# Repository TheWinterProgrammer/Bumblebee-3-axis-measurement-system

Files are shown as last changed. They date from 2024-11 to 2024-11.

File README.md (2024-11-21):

# Bumblebee 3-Axis Measurement System

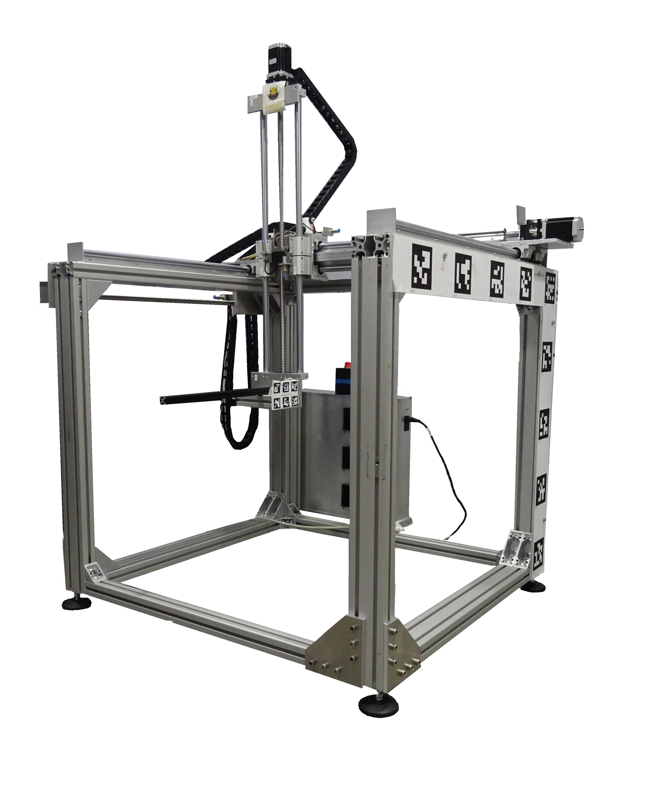
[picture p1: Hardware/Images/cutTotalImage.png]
  

## Overview

The **Bumblebee 3-Axis Measurement System** is a versatile, open-source, cubic positioning robot adapted for low-field MRI research. This project builds upon the design of the original [COSI Measure Robot](https://www.opensourceimaging.org/project/cosi-measure/), enhancing its mechanical and electronic capabilities. The system was redesigned during the 2023-2024 academic year as part of several bachelor theses at our institute.

### Key Features
- **Adapted Mechanical Design**  
  The robot is designed for:
  - A larger measurement volume.
  - Improved efficiency relative to the robot's size.

- **Simplified Electronics**  
  Replacing the BeagleBone Black and embedded Linux system, the new design features:
  - An **Arduino MEGA** as the central microcontroller for motor control, limit switch evaluation, and serial communication.
  - A **Python-based host PC script** to:
    - Control mapping.
    - Communicate positions to the robot.
    - Interface with the Hall sensor.

- **Sensor Integration**  
  The current setup uses the **F.W. BELL Series 9900 Hall sensor** with the ZOA99-3208 3D Hall probe. The Python script processes data from this sensor via serial communication. However, the system can accommodate other sensors as needed.

---

## Publication

This work was presented and published as a conference paper:  
**Samlow J, Maltsev S [TheWinterProgrammer](https://github.com/TheWinterProgrammer), Buckenmaier K, Scheffler K, Povolni P [ppolGTMonster](https://github.com/ppolGTMonster) (2024). Easy Rebuildable Cubic 3-Axis Positioning Robot Based on Open-Source Hardware: Validated via Camera-Based Motion Tracking and Initial Application in Magnetic Low Field Mapping.** *DACH-ISMRM 2024 Program & Proceedings, Tübingen, Germany*, pp. 1–2.

---

## Getting Started

There a tree major parts:

### System Components
1. **Hardware** [here](Hardware)
   - Rebuilt mechanical design for larger volume mapping.
   - Compact yet efficient cubic robot frame.

2. **Electronics** 
   - Arduino MEGA for robot control and interfacing [here](Software/Arduino/).
   - Support for various sensors through serial communication.

3. **Software** [here](Software/PythonGUI/)
   - Python script to manage mapping and communication.

### Usage
1. Set up the Arduino MEGA and connect the motors, limit switches, and Hall sensor.
2. Run the Python script on the host PC for:
   - Position control of the robot.
   - Real-time data collection from the Hall sensor.

---
## Author
   - Judith Samlov ([E-Mail](judith.samlov@tuebingen.mpg.de)), (Hardware and Software) 
   - Pavel Povolni ([E-Mail](pavel.povolni@tuebingen.mpg.de), [Github](https://github.com/ppolGTMonster)), (Hardware and Software)
   - Sergej Maltsev ([E-Mail](sergej.maltsev@tuebingen.mpg.de), [Github](https://github.com/TheWinterProgrammer)), (Software Python GUI)

### Contact
For further inquiries or contributions, feel free to reach out through the repository.

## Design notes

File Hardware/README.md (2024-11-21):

# Hardware

## Assembly Robot

The assembly of the robot, including all CAD design files and instructions, is thoroughly described and documented in the following resources:  
- [COSI Measure Project Page](https://www.opensourceimaging.org/project/cosi-measure/)  
- [COSI Measure GitHub Repository](https://github.com/opensourceimaging/cosi-measure/tree/master/Mechanical%20System)  

We recommend referring to these resources for detailed instructions. The hardware components for the drive and ordering details are also described there.

### Key Components for 3D Drive
We used the following parts for the 3D drive. These may be relevant if adapting the PCB, though similar drives should also work:

- **Motor**: NEMA23 60HS88, 3 pieces (no longer available)  
  Alternative: [HYBRID NEMA-23 Stepper Motor](https://www.reichelt.de/hybridschrittmotor-nema-23-1-8-4-2-a-2-52-v-act-23hs9440-26-p316758.html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)  
- **Motor Driver**: ACT DM542, 3 pieces  
  Link: [Stepper Motor Driver ACT DM542](https://www.reichelt.de/schrittmotortreiber-fuer-nema-23-18-50-v-act-dm542-p237924.html?&trstct=pos_1&nbc=1)  
- **Limit Switch**: LJ12A3-4-Z/BX DC6-36V, 3 pieces  
  Link: [Inductive Sensor](https://www.roboter-bausatz.de/p/induktiver-sensor-lj12a3-4-z-bx-dc6-36v?number=RBS11420)  
- **Power Source**: 36V, 9.75A (350W)  
  Link: [36V Power Supply](https://www.reichelt.de/schaltnetzteil-geschlossen-351-w-36-v-9-75-a-mw-uhp-350-36-p256082.html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)  

---

## Assembly PCB

### General

For this version of COSI Measure, we used an **Arduino Mega** as the central microcontroller (µC).  

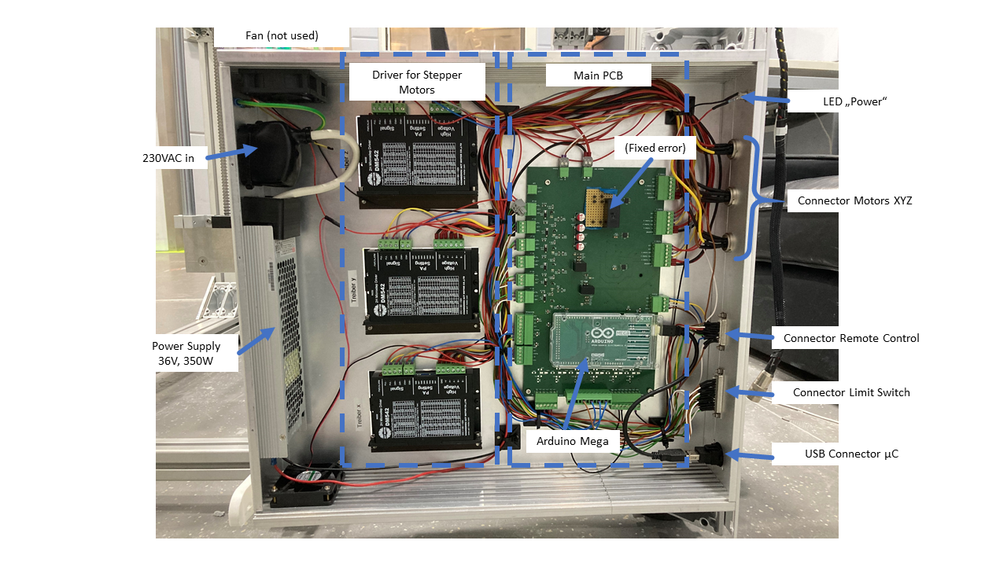
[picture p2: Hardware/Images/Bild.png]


While assembling, some errors in the V1.0 PCB design were identified and corrected in version V2.0, which is made available here.  

This design uses a two-part concept:  
1. **Main PCB**  
2. **Optional Remote Control**  
   - The remote control can manually adjust the Hall sensor's position. Although the remote control functionality was disabled in this setup, the buttons and encoders remain available in the hardware. Manual control has been replaced by Python-based software control.

If needed, you can design your own remote control and connect it via the 26-pin SubD connector.

### Implemented Functions

- Control of 3 stepper motors via PWM signals.  
- Safety circuit with emergency stop to disconnect motor drivers' power supply.  
- I2C output, e.g., for display integration.  
- Serial communication (USB) with the host PC.  
- Other analog inputs/outputs are available and can be used e.g. for additional sensors.

### PCB Design
- Designed using **KiCad 8** (no additional packages required).  
- Comments in the schematic provide explanatory details.  
- Uses large SMD components (e.g., SMD1206 for resistors and capacitors) for easy soldering.  
- Two-layer PCB design to reduce manufacturing costs.  
- A bill of materials (BoM) is included in the accompanying Excel sheet.  

#### Note
The PCB size can be reduced by modifying component footprints and minimizing unused connectors.

### Assembly PCB
- Large component sizes simplify soldering.  
- Arduino Mega connects via pin headers for easy replacement.  
- A cutout in the PCB allows visibility of the Arduino's built-in LED when mounted.  

### Wiring Inside the Case
The PCB, power supply, and motor drivers are all housed in a single case. Wiring is straightforward with labeled connectors on the PCB. **Phoenix 3.81mm PCB connectors** were used to facilitate cable attachment.  

#### ⚠️ Important Safety Note:
<span style="color: red;">- The power supply operates at 230V AC, which is **extremely dangerous**.</span>  
<span style="color: red;">- Electrical connections between the power input and power supply are **not documented here**.</span>  
<span style="color: red;">- **Only a qualified electrician** should handle this part. Ensure the case is grounded and use an FI-protected socket.</span>

---

## Assembly Case for Electronics

### Case Design
The case is a standard **19-inch, 2 height units** enclosure. The side profiles, front and back panels, and top and bottom panels were milled using a mechanical workshop.  

For best results, the front and back panels should be milled. Alternatively, mounting holes can be created manually. Accuracy is essential for mounting the DSub connector.  

Cooling: Two 12V fans were installed but found unnecessary during operation. Drivers were mounted on the base plate with cooling fins extending outward for heat dissipation. However, this may not be required.

### CAD Files
The case design was created using **Autodesk Inventor 2022**.  
- Files are exported as STEP files for compatibility with other CAD programs.  
- Side profiles are customizable, depending on the electronics installed.  

### Front Connections
All parts for the front panel are listed in the BoM.  
- **USB**: For Arduino Mega-PC serial communication.  
- **Limit Switches**: 25-pin Sub-D (male) for connecting up to 6 limit switches.  
- **Remote Control**: 26-pin Sub-D (female).  
- **Motor Connections**: 4-pin DIN connectors (male) for X, Y, and Z-axis motors.  
- **Power LED**: Indicates power supply status.  
- **Emergency Stop**: Cuts power to motor drivers via relay.  

### Back Connections
- **230V IEC Plug**: Includes an on/off switch and main fuse (1.75A, slow-blow).  

### Wiring
Wiring is simplified by labeled PCB connectors and depends on the components installed. For questions, please contact us.

---

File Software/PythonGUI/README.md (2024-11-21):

# Python GUI Software

## Overview

This script opens a GUI to operate the **3-Axis Measurement System**, create a measurement point structure, and evaluate a measured magnetic field.

### Key Features
- **Adapted Program Design**  
  This Program is designed for:
  - Movement of the Robot, by a Serial connection.
  - Creation of a point array for different shapes.
  - Automatic measurement of the points array with also saves the Hall sensor data.
  - An optional activation of a Relay during the measurement, e.g. to measure a current dependent system.
  - Evaluation of a measurement with plot a histogram of the gradient magnetic field or a homogeneous field.

- **Tab Design**  
  The Tabs in this Program are designed like:
  - **Measurement Tab**: This Tab controls the robot, relay and Hall sensor by 3 different Serial connections:  
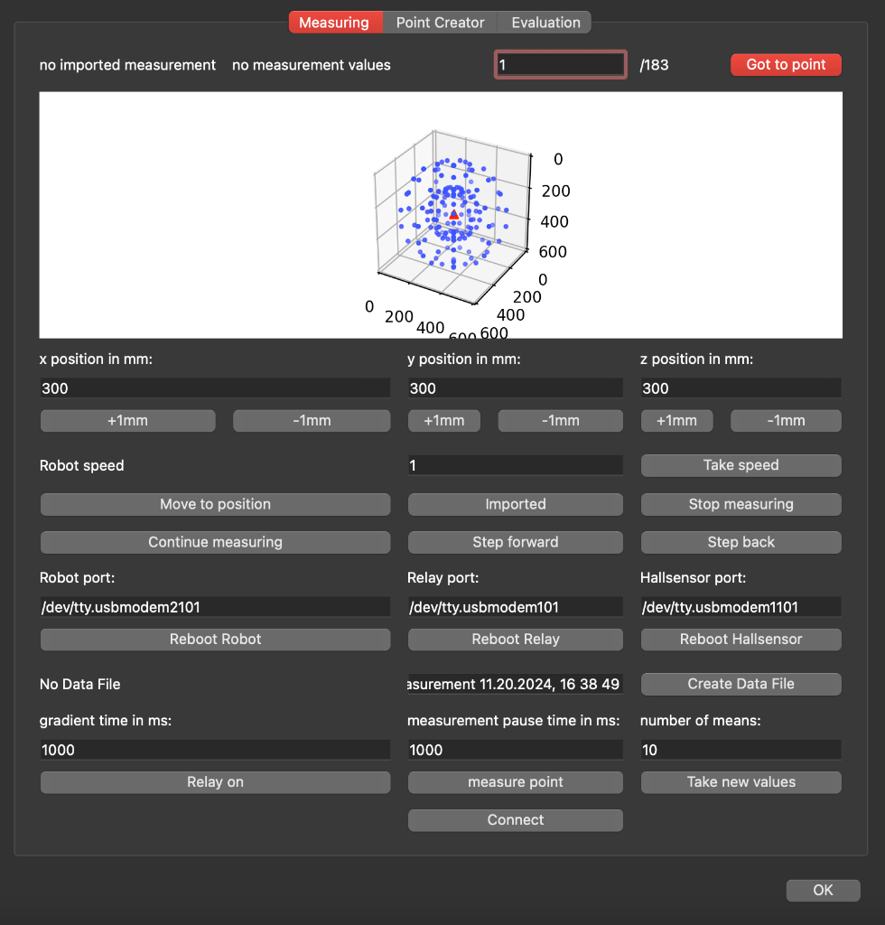
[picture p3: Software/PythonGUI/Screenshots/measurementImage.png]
      
  - **Point Creator Tab**: This Tab creates a Measurement CSV file, which can be implemented into the Measurement Tab, to start a measurement through it:  
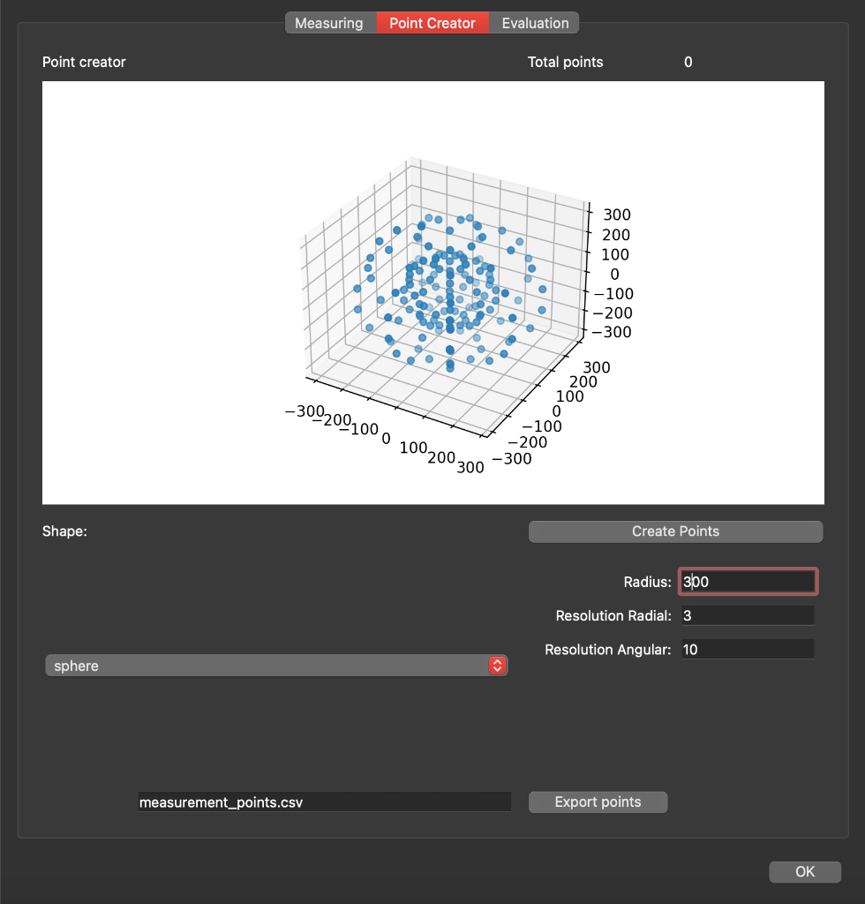
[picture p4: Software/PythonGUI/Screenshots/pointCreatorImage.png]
      
  - **Evaluation Tab**: In this Tab you can make a simple evaluation:  
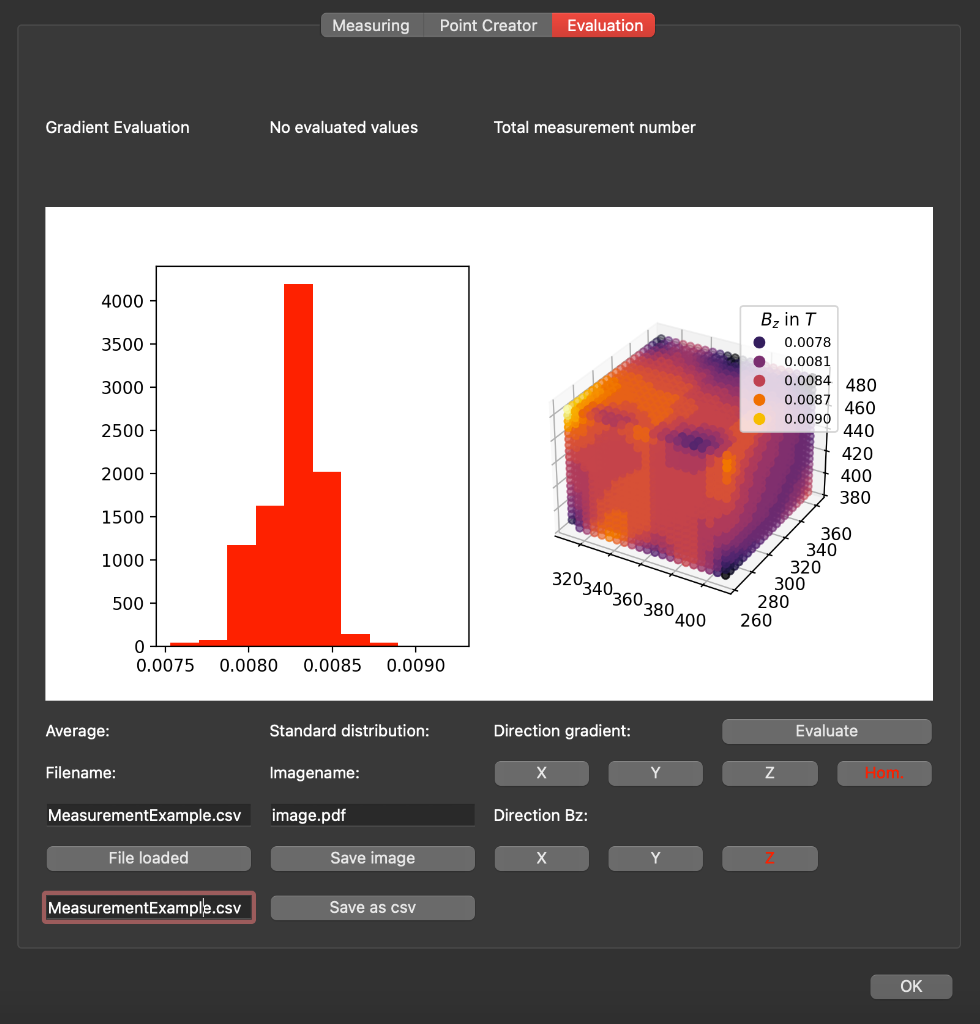
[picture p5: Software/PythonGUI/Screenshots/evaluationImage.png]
      

## Get Started

You need Python **3.8** or newer. Follow these steps to set up and run the software:

### 1. Create a Virtual Environment (Recommended)

1. Open your terminal or command prompt.
2. Navigate to the project directory:
   ```bash
   cd path/to/project
   ```

3. Create a virtual environment:
  ```bash
  python3 -m venv myenv
  ```

4. Activate the virtual environment:
 - On macOS/Linux:
    ```bash
    source myenv/bin/activate
    ```

- On Windows:
    ```bash
    myenv\Scripts\activate
    ```

### 2. Get the required libraries
Download the required libraries:
```bash
pip install -r requirements.txt
```
### 3. Run the Software
1. Start the program with the following command:
  ```bash
  python ALFRobotSoftware.py
  ```
  or
  ```bash
  python3 ALFRobotSoftware.py
  ```

2. The GUI will open, and you can begin using the application.

### Contact
For further inquiries or contributions, feel free to reach out through the repository.

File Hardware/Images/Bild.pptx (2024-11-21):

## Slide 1

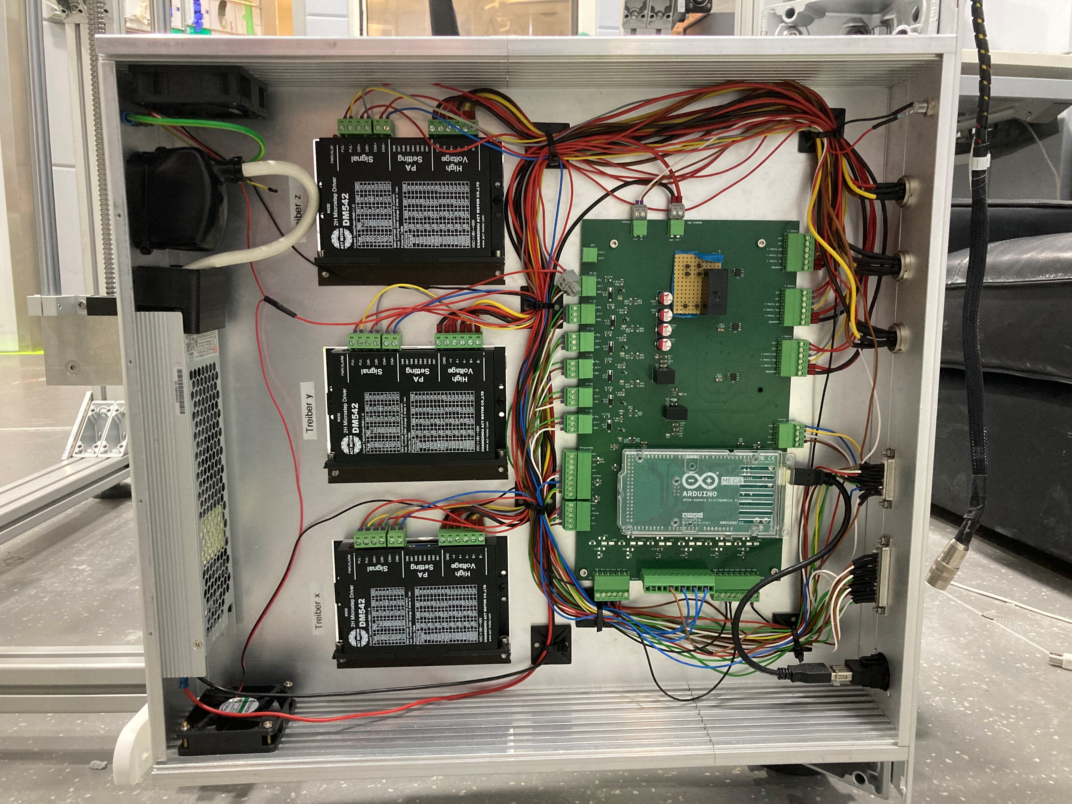
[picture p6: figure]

Fan (not used)

Driver for Stepper Motors

Main PCB

Arduino Mega

LED „Power“

(Fixed error)

230VAC in

Connector Motors XYZ

Connector Remote Control

Power Supply
36V, 350W

Connector Limit Switch

USB Connector µC

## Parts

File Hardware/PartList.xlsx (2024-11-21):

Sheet: PCB
Order list for electronic components
ID | Part-Info | Manufacturer | Part# Manufacturer | Part# Mouser | Amount | Comment
U1 | DCDC 12V, 2A | CUI Inc | P7812-2000-S | 490-P7812-2000-S | 1 | could be any cheaper option
U2 | DCDC 5V, 2A | TRACO Power | TSR 2-2450 | 495-TSR2-2450 | 1 | could be any cheaper option
K3 | Relais 12V, 16A | CUI Devices | PR22-12V-400-1A | 179-PR22-12V-400-1A | 1
D6, D9, D10, D13, D14, D17, D18 | Zener Diode 5.1V | Diodes Inc | SMAZ5V1-13-F | 621-SMAZ5V1-F | 7
D30,D24.D23,D31,D25,D29,D22,D27,D21,D26,D19,D28 | Zener Diode 5.1V | -''- | -''- | -''- |  | Backup Place, if needed
C4,C3,C1,C2 | Pol C 100uF, 50V | Wurth Electronic | 865080653016 | 710-865080653016 | 4
C10,C5,C11, C14,C33,C13,C12,C32,C31 | C 100nF, SMD1206 | KEMET | C1206C104M5RACTU | 80-C1206C104M5R | 9
C36,C34,C35,C6 | C 10nF, SMD1206 | Wurth Electronic | 885012208112 | 710-885012208112 | 4
C8,C7 | C 22uF, SMD1206 | Murata | GRM31CC71E226ME15L | 81-GRM31CC71E226ME5L | 2
C9 | C 10uF, SMD1206 | Samsung Electro-Mechanics | CL31A106KAHNNNF | 187-CL31A106KAHNNNF | 1
Q1, Q4,Q3,Q6,Q2,Q5,Q7 | nFET, 60V, 300mA | Vishay | 2N7002K-T1-GE3 | 781-2N7002K-GE3 | 7 | could be any cheaper option
D5,D2,D3,D1 | LED Blue, SMD0603 | Wurth Electronic | 150060BS75000 | 710-150060BS75000 | 4
D11,D12 | LED Red, SMD0603 | Wurth Electronic | 150060RS75000 | 710-150060RS75000 | 2
D16,D15 | LED Green, SMD0603 | Wurth Electronic | 150060GS75000 | 710-150060GS75000 | 2
D8,D7 | LED Yellow, SMD0603 | Wurth Electronic | 150060YS75000 | 710-150060YS75000 | 2
U3,U4,U5 | Current Sensor | Texas Instruments | TMCS1107A4BQDT | 595-TMCS1107A4BQDT | 3
D4 | Diode, SMD1206, 1A | Comchip Technology | CURN105-HF | 750-CURN105-HF | 1
R7, R11,R10,R8,R12,R9,R13 | R 10kOhm, SMD1206 | ROHM Semicon | SFR18EZPJ103 | 755-SFR18EZPJ103 | 7 | could be any cheaper option, aslo smaller if PCB is redesigned
R6 | R 82kOhm, SMD1207 | Bourns | CR1206-JW-823ELF | 652-CR1206JW-823ELF | 1 | could be any cheaper option, aslo smaller if PCB is redesigned
R1,R5 | R 1.8kOhm, SMD1208 | Bourns | CR1206-FX-1801ELF | 652-CR1206FX-1801ELF | 2 | could be any cheaper option, aslo smaller if PCB is redesigned
R4, R26,R35,R27,R18,R19,R34 | R 470kOhm, SMD1209 | Bourns | CR1206-FX-4703ELF | 652-CR1206FX-4703ELF | 7 | could be any cheaper option, aslo smaller if PCB is redesigned
R2 | R 500Ohm, SMD1210 | Vishay | MCA12060D5000BP500 | 594-MCA12060D5000BP5 | 1 | could be any cheaper option, aslo smaller if PCB is redesigned
R33,R3,R32 | R 100Ohm, SMD1211 | Bourns | CR1206-JW-101ELF | 652-CR1206JW-101ELF | 3 | could be any cheaper option, aslo smaller if PCB is redesigned
R14,R15,R30,R23,R31,R22 | R 1kOhm, SMD1212 | Vishay | CRCW12061K00JNEAC | 71-CRCW12061K00JNEAC | 6 | could be any cheaper option, aslo smaller if PCB is redesigned
R25,R24,R16,R17 | R 150Ohm, SMD1213 | Bourns | CR1206-JW-151ELF | 652-CR1206JW-151ELF | 4 | could be any cheaper option, aslo smaller if PCB is redesigned
R21,R28,R20,R29,R36,R37 | R 49.9kOhm, SMD1214 | Yageo | RT1206FRE0749K9L | 603-RT1206FRE0749K9L | 6 | could be any cheaper option, aslo smaller if PCB is redesigned
Ard1 | Arduino Mega | Arduino | A000067 | 782-A000067 | 1 | could be any cheaper option
Connectors
J10, J11, J5, J8 (Male) | 2pin | Phoenix Contact | 1803277 | 651-1803277 | 4 | PCB Thorugh Hole Mount
Female |  | Phoenix Contact | 1803578 | 651-1803578 | 4 | Wire Mount
J12, J13, J14, J15, J16, J17 (Male) | 3pin | Phoenix Contact | 1803280 | 651-1803280 | 6 | PCB Thorugh Hole Mount
Female |  | Phoenix Contact | 1803581 | 651-1803581 | 6 | Wire Mount
J1 (Male) | 4pin | Phoenix Contact | 1803293 | 651-1803293 | 1 | PCB Thorugh Hole Mount
Female |  | Phoenix Contact | 1803594 | 651-1803594 | 1 | Wire Mount
J19 (Male) | 5pin | Phoenix Contact | 1803303 | 651-1803303 | 1 | PCB Thorugh Hole Mount
Female |  | Phoenix Contact | 1803604 | 651-1803604 | 1 | Wire Mount
J2, J6, J7, J9 (Male) | 6pin | Phoenix Contact | 1803316 | 651-1803316 | 4 | PCB Thorugh Hole Mount
Female |  | Phoenix Contact | 1803617 | 651-1803617 | 4 | Wire Mount
J4, J18 (Male) | 8pin | Phoenix Contact | 1803332 | 651-1803332 | 2 | PCB Thorugh Hole Mount
Female |  | Phoenix Contact | 1803633 | 651-1803633 | 2 | Wire Mount
J3 | 12pin | Phoenix Contact | 1803374 | 651-1803374 | 1 | PCB Thorugh Hole Mount
Female |  | Phoenix Contact | 1803675 | 651-1803675 | 1 | Wire Mount
Pin Header Arduino Mega
 | 1 Row, 10pin | Amphenol | 10129378-910002BLF | 649-1012937891002BLF | 1
 | 1 Row, 8pin | Amphenol | 10129378-908002BLF | 649-1012937890802BLF | 5
 | 2 Row, 36pin | Amphenol | 77313-424-36LF | 649-77313-424-36LF | 1
Backup for extra outputs of µC
C25,C19,C20,C26,C21,C27,C17,C24,C23,C15,C18,C22 | SMD1206 | na |  |  |  | Backup Place, if needed
R53,R58,R73,R56,R55,R71,R57,R69,R54,R68,R72,R76,R49,R51,R74,R46,R75,R70,R44,R47,R63,R40,R45,R50,R52,R60,R66,R65,R62,R38,R64,R61,R67,R41,R59,R42 | SMD1206 | na |  |  |  | Backup Place, if needed
D30,D24.D23,D31,D25,D29,D22,D27,D21,D26,D19,D28 | Zener Diode 5.1V | -''- | -''- | -''- |  | Backup Place, if needed

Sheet: Case
Order list for electronic components
Info | Part-Info | Manufacturer | Part# Manufacturer | Part# RS Components | Amount | Comment
Connector Limit Switches | Sub D, 25pin, Male | RSPro | 544-3806 | 544-3806 | 1
Connector Remote Control | Sub D, 26pin, Female | Amphenol | 10090770-S264ALF | 173-8753 | 1
Connector Motor | DIN, 4pin, Male | Amphenol | C091-31W004-1002 | 157-2691 | 3
LED Mount Power | with Thread | Mentor | RTM5030 | 283-6561 | 1
USB Connector | Panel Mount, Type B | RS Pro | 862-1573 | 862-1573 | 1
Emergency Switch |  | Deca | B1E04-E620R-F11 | 282-1476 | 1 | Could be any cheaper type
IEC Power Connector | 230V In | RS Pro | 811-7216 | 811-7216 | 1 | Take care, 230V are dangerous!

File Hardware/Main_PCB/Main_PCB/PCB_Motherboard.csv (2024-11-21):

ID | Bezeichner | Footprint | Stückzahl | Bezeichnung | Anbieter und Referenz
1 | R53,R58,R73,R56,R55,R71,R57,R69,R54,R68,R72,R76,R49,R51,R74,R46,R75,R70,R44,R47,R63,R40,R45,R50,R52,R60,R66,R65,R62,R38,R64,R61,R67,R41,R59,R42 | R_1206_3216Metric_Pad1.30x1.75mm_HandSolder | 36 | R
2 | C14,C33,C13,C12,C32,C31 | C_1206_3216Metric_Pad1.33x1.80mm_HandSolder | 6 | 100 n
3 | J17 | PhoenixContact_MC_1,5_3-G-3.81_1x03_P3.81mm_Horizontal | 1 | Limit-Switch y2
4 | Q4,Q3,Q6,Q2,Q5,Q7 | SOT-23 | 6 | Q_NMOS_GDS
5 | J2 | PhoenixContact_MC_1,5_6-G-3.81_1x06_P3.81mm_Horizontal | 1 | Motordriver X
6 | J19 | PhoenixContact_MC_1,5_5-G-3.5_1x05_P3.50mm_Horizontal | 1 | Terminal_Encoder
7 | J5 | PhoenixContact_MC_1,5_2-G-3.81_1x02_P3.81mm_Horizontal | 1 | Terminal_12V
8 | D5,D2,D3,D1 | LED_0603_1608Metric_Pad1.05x0.95mm_HandSolder | 4 | blue
9 | C25,C19,C20,C26,C21,C27,C17,C24,C23,C15,C18,C22 | C_1206_3216Metric_Pad1.33x1.80mm_HandSolder | 12 | C
10 | R14,R15,R30,R23,R31,R22 | R_1206_3216Metric_Pad1.30x1.75mm_HandSolder | 6 | 1k
11 | J18 | PhoenixContact_MC_1,5_8-G-3.81_1x08_P3.81mm_Horizontal | 1 | Terminal Buttons
12 | C10,C5,C11 | C_1206_3216Metric_Pad1.33x1.80mm_HandSolder | 3 | 100n
13 | J3 | PhoenixContact_MC_1,5_12-G-3.81_1x12_P3.81mm_Horizontal | 1 | Erstaz_Terminal
14 | R26,R35,R27,R18,R19,R34 | R_1206_3216Metric_Pad1.30x1.75mm_HandSolder | 6 | 470 k
15 | K3 | Relay_PR22 | 1 | PR22
16 | D30,D14,D13,D24,D18,D17,D23,D9,D31,D10,D25,D29,D22,D6,D27,D21,D26,D19,D28 | D_SMA_Handsoldering | 19 | 5,1V
17 | J16 | PhoenixContact_MC_1,5_3-G-3.81_1x03_P3.81mm_Horizontal | 1 | Limit-Switch x2
18 | J10 | PhoenixContact_MC_1,5_2-G-3.81_1x02_P3.81mm_Horizontal | 1 | EmergencyStop
19 | C36,C34,C35,C6 | C_1206_3216Metric_Pad1.33x1.80mm_HandSolder | 4 | 10n
20 | J9 | PhoenixContact_MC_1,5_6-G-3.81_1x06_P3.81mm_Horizontal | 1 | Motordriver Z
21 | R21,R28,R20,R29,R36,R37 | R_1206_3216Metric_Pad1.30x1.75mm_HandSolder | 6 | 50k
22 | U3,U4,U5 | SOIC-8_3.9x4.9mm_P1.27mm | 3 | ACS715xLCTR-20A
23 | R25,R24,R16,R17 | R_1206_3216Metric_Pad1.30x1.75mm_HandSolder | 4 | 150
24 | J11 | PhoenixContact_MC_1,5_2-G-3.81_1x02_P3.81mm_Horizontal | 1 | Terminal Power
25 | C4,C3,C1,C2 | CP_Elec_8x6.2 | 4 | 100u
26 | D8,D7 | LED_0603_1608Metric_Pad1.05x0.95mm_HandSolder | 2 | yellow
27 | R11,R10,R8,R12,R9,R13 | R_1206_3216Metric_Pad1.30x1.75mm_HandSolder | 6 | 10k
28 | J13 | PhoenixContact_MC_1,5_3-G-3.81_1x03_P3.81mm_Horizontal | 1 | Limit-Switch x1
29 | D11,D12 | LED_0603_1608Metric_Pad1.05x0.95mm_HandSolder | 2 | red
30 | J7 | PhoenixContact_MC_1,5_6-G-3.81_1x06_P3.81mm_Horizontal | 1 | Motordriver Y
31 | C8,C7 | C_1206_3216Metric_Pad1.33x1.80mm_HandSolder | 2 | 22u
32 | J4 | PhoenixContact_MC_1,5_8-G-3.81_1x08_P3.81mm_Horizontal | 1 | Terminal_GND
33 | C9 | C_1206_3216Metric_Pad1.33x1.80mm_HandSolder | 1 | 10u
34 | J14 | PhoenixContact_MC_1,5_3-G-3.81_1x03_P3.81mm_Horizontal | 1 | Limit-Switch y1
35 | K1 | Relay_SPST_Schrack-RT1-16A-FormA_RM5mm | 1 | PR22-12V-400-1A
36 | J12 | PhoenixContact_MC_1,5_3-G-3.81_1x03_P3.81mm_Horizontal | 1 | Limit-Switch z1
37 | J15 | PhoenixContact_MC_1,5_3-G-3.81_1x03_P3.81mm_Horizontal | 1 | Limit-Switch z2
38 | U1 | P7812 | 1 | P7812
39 | D16,D15 | LED_0603_1608Metric_Pad1.05x0.95mm_HandSolder | 2 | green
40 | J1 | PhoenixContact_MC_1,5_4-G-3.81_1x04_P3.81mm_Horizontal | 1 | Terminal_Display
41 | U2 | P7812 | 1 | V7805
42 | R33,R3,R32 | R_1206_3216Metric_Pad1.30x1.75mm_HandSolder | 3 | 100
43 | R1,R5 | R_1206_3216Metric_Pad1.30x1.75mm_HandSolder | 2 | 1,8k
44 | R2 | R_1206_3216Metric_Pad1.30x1.75mm_HandSolder | 1 | 500
45 | J6 | PhoenixContact_MC_1,5_6-G-3.81_1x06_P3.81mm_Horizontal | 1 | Terminal_5V
46 | J8 | PhoenixContact_MC_1,5_2-G-3.81_1x02_P3.81mm_Horizontal | 1 | Terminal Power BU
47 | D4 | D_1206_3216Metric_Pad1.42x1.75mm_HandSolder | 1 | D
48 | R4 | R_1206_3216Metric_Pad1.30x1.75mm_HandSolder | 1 | 470k
49 | Q1 | SOT-23 | 1 | Q_NMOS_GSD
50 | R7 | R_1206_3216Metric_Pad1.30x1.75mm_HandSolder | 1 | 10 k
51 | Ard1 | Arduino-Mega | 1 | Arduino_Mega
52 | R6 | R_1206_3216Metric_Pad1.30x1.75mm_HandSolder | 1 | 82 k

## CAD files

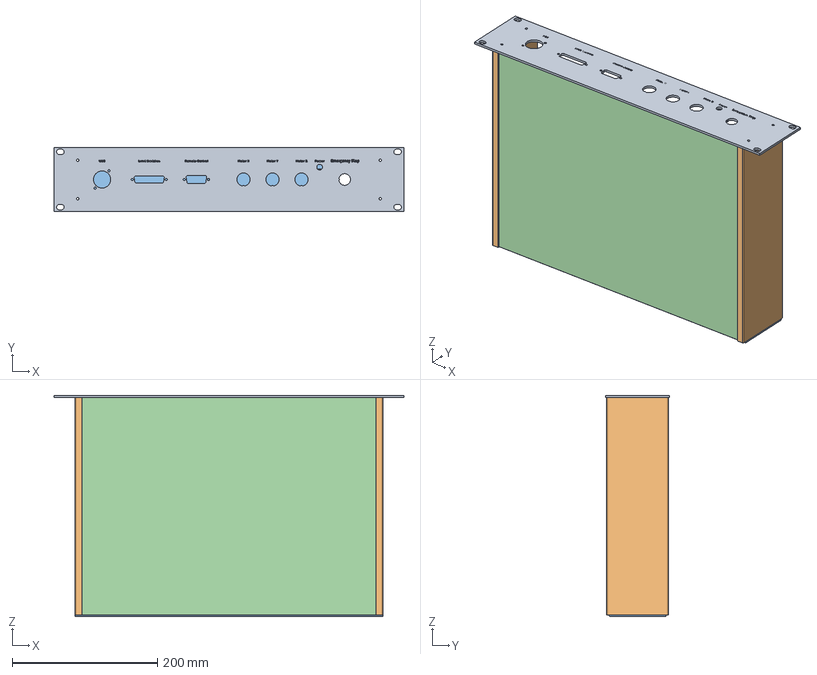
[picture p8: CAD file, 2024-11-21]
Hardware/Case/Case_Assembly.stp
482.6 x 88.1 x 305.0 mm
Case_Front
Case_Side x 2
Case_Back
Case_Top

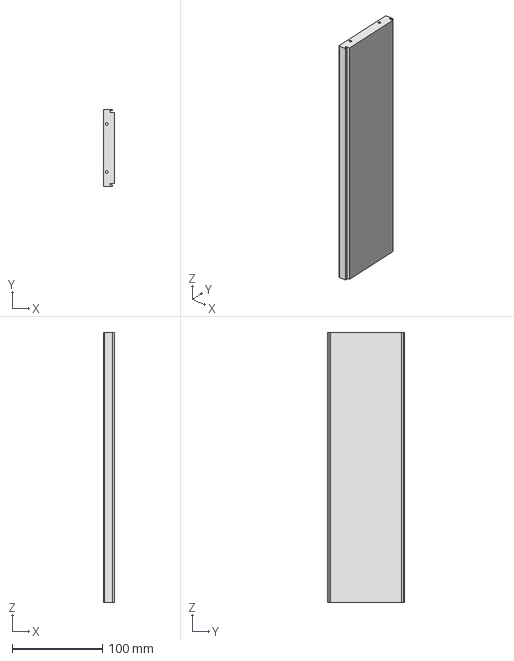
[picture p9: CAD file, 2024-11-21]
Hardware/Case/Case_Side.stp
12.5 x 86.0 x 300.0 mm

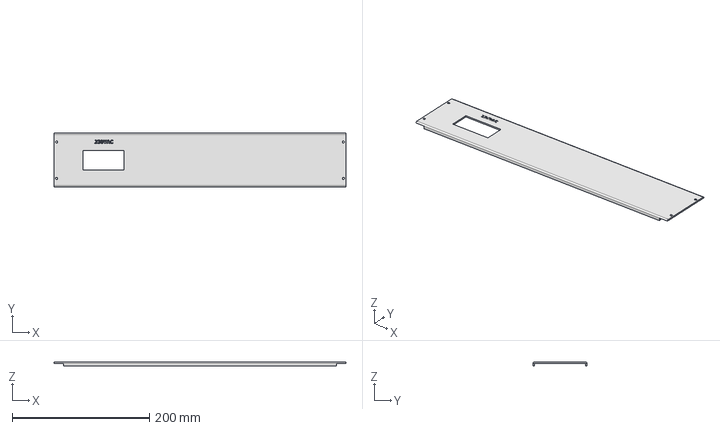
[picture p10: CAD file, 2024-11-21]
Hardware/Case/Case_Back.stp
425.0 x 78.9 x 6.00 mm

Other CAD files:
Hardware/Case/Case_Assembly.iam
Hardware/Case/Case_Back.ipt
Hardware/Case/Case_Front.ipt
Hardware/Case/Case_Side.ipt
Hardware/Case/Case_Top.ipt

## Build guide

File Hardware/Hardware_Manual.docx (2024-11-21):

Instructions to rebuild the Hardware

Project

Judith Samlow, Sergej Maltsev, Pavel Povolni

November 2024

# 1 Preamble

As part of the low-field MRI research at our institute, the already known positioning robot „COSI Measure“ was rebuilt in 2023-2024 as part of several bachelor theses:

https://www.opensourceimaging.org/project/cosi-measure/

The mechanical design was a bit adapted to our needs, which is more or less a bit bigger measured Volume and a bit higher efficiency of the robot size.

The biggest change to published work was a redesign of the electronics part:

In contrast to the Beagle Bone Black with embedded Linux used back than with the original robot, we have chosen a much simpler design:

- The central µC is an Arduino MEGA. It controls the motors, evaluates the limit switches and communicates with a host PC via a serial interface
- A Python script runs on the host PC, which controls the mapping, serially communicates the new position to be approached by the robot and simultaneously communicates with a Hall sensor

In our case, the F.W. BELL Series 9900 Hall sensor with the ZOA99-3208 3D Hall probe was used. This sensor also has a serial output, which was evaluated with the running Python script.

In principle, however, this setup should allow the integration of any other sensor.

This work was presented and published as a conference paper:

Samlow J, Maltsev S, Buckenmaier K, Scheffler K, Povolni P (2024) Easy Rebuildable Cubic 3-Axis Positioning Robot Based on Open-Source Hardware: Validated via Camera-Based Motion Tracking and Initial Application in Magnetic Low Field Mapping. DACH-ISMRM 2024 Program & Proceedings. Tübingen, Germany, pp 1–2

# 2 Hardware

## 2.1 Assembly Robot

The assembly of the robot with all CAD design files & instructions is very well described and documented:

https://www.opensourceimaging.org/project/cosi-measure/

https://github.com/opensourceimaging/cosi-measure/tree/master/Mechanical%20System

Therefore, we refer at this point to the original Github. The used hardware of the drive and place to order them is also described there

However, we used the following parts for the 3D Drive (which is maybe important regarding the build PCB. However, it should be possible to attach any similar drive)

We used:

- Motor: NEMA23 60HS88, 3 pieces No longer available, but this type should work just as well: https://www.reichelt.de/hybridschrittmotor-nema-23-1-8-4-2-a-2-52-v-act-23hs9440-26-p316758.html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
- Motor driver: ACT DM542, 3 pieces Link: https://www.reichelt.de/schrittmotortreiber-fuer-nema-23-18-50-v-act-dm542-p237924.html?&trstct=pos_1&nbc=1
- Limit Switch: LJ12A3-4-Z/BX DC6-36V, 3 pieces Link: https://www.roboter-bausatz.de/p/induktiver-sensor-lj12a3-4-z-bx-dc6-36v?number=RBS11420
- Power source: 36V, 9.75A (350W) Link: https://www.reichelt.de/schaltnetzteil-geschlossen-351-w-36-v-9-75-a-mw-uhp-350-36-p256082.html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

## 2.2 Assembly PCB’s

### 2.2.1 General

In our version of COSI Measure, an Arduino Mega was used as the central microcontroller (µC).

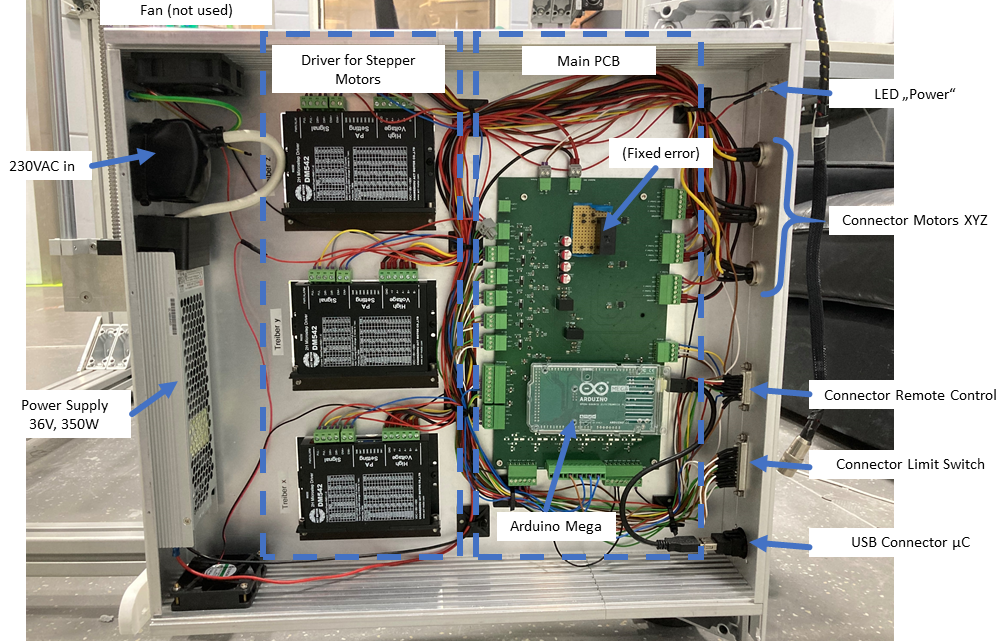
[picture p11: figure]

There were a few errors in the built circuit board (V1.0) that were fixed during the assembly of our robot. However, we fixed these errors in the V2.0 circuit board, which we made available here.

A two-part concept was developed.

In addition to the main PCB, a remote control was built that could be used to manually change the position of the Hall sensor. The connection of the buttons, encoders, etc. is still present in the hardware and can be used again without any problems. In the option presented here, the remote control was deactivated and no longer used. The same task was done using the software control in the running Python script.

If necessary, you can design the remote control according to your own needs and connect it to the 26-pin SubD connector in the case.

### 2.2.2 Implemented Functions

- Control of 3 stepper motors via PWM signals
- Safety circuit: both the µC and an emergency stop disconnect the power supply to the motor drivers
- I2C output, e.g. for a display
- Serial communication (USB) with host PC
- Other analog inputs/outputs are available and can be used e.g. for additional sensors

### 2.2.3 CAD PCB

The PCB was designed with the free software KiCad 8. No further packages are necessary. Comments in the schematic should explain the design.

For easy soldering of the PCB, all SMD components are selected as large as possible, e.g. SMD1206 for resistors and capacitors.

If you wish you can change that and adapt the footprints to the sizes you want. Then you would need to relayout the PCB

The PCB is designed in two layers to keep manufacturing costs low. The board size can be significantly reduced by adapting the footprints and possibly also by reducing the number of connectors required.

The BoM of all components is included in the attached Excel list.

### 2.2.4 Assembly PCB

The assembly should not be a major problem due to the large component sizes that were chosen.

The Arduino Mega is simply plugged onto the soldered pin headers and can thus be easily replaced if necessary.

A cutout is provided in the circuit board at the location of the LED so that the built-in LED of the Arduino can be seen I mounted state

### 2.2.5 Wiring inside the Case

Die Platine, das Netzteil, sowie die 3 Motortreiber sind alle im selben Gehäuse verbaut. Die Verkabelung ist durch die beschrifteten Stecker auf der Platine einfach möglich.

Es wurden Phönix 3.81mm Leiterplattenverbinder genutzt. Die Kabel können so einfach in den Schraubklemmen befestigt werden.

ACHTUNG!

Das Netzteil wird mit 230V betrieben! 230VAC sind lebensgefährlich!

Daher beschreiben wir die elektrische Verbindung zwischen Spannungseingang und Netzteil nicht!

Sucht euch für diesen Teil einen erfahrenen Elektriker mit entsprechender Ausbildung!

Denkt daran das Gehäuse zu erden und nur an einer FI-geschützten Steckdose zu betreiben!

The PCB, the power supply and the three motor drivers are all installed in the same case. The wiring cab be easily done through the labeled connectors on the PCB.

Phoenix 3.81mm PCB connectors were used. The needed wires can be easily attached to the screw terminals.

ATTENTION!

The power supply is operated at 230V!

230VAC is extremely dangerous!

Therefore, we do not describe the electrical connection between the voltage input and the power supply!

For this part, find an experienced electrician with the appropriate training!

Remember to ground the housing and only operate it on a FI-protected socket!

## 2.3 Assembly Case for Electronics

### 2.3.1 Case

The case is a standard 19-inch case with a side profile of 2 height units. The side profiles, front and back panels, top and bottom panels were milled by us in your mechanical workshop.

The front and back should be milled for best results.

At the same time, however, it is also possible to create the mounting holes by hand. Special accuracy is not required (in this case, pay attention to the mounting of the DSub connector).

We had also installed two 12V fans in our case to cool the internal electronics if necessary. This was not needed in the end and the fans were never on.

The motor drivers are mounted on the base plate, with the cooling fins of the drivers protruding through the base to the outside, in order to dissipate the heat. From experience, we think that this is not necessary and that a simpler design is possible with the drivers inside the case

### 2.3.2 CAD

The CAD of the case was created in Autodesk Inventor 2022. All files were exported in Step-files and should be able to be imported in any CAD program.

The side profiles are only hinted at here!

These side profiles are sold on meter basis and can be cut by you to your desired size…. Depending on which electronics you have installed in the case.

### 2.3.3 Front Connections

All parts that are built into the front are listed in the BoM list

- USB: USB socket connected to the Arduino Mega (connection to the PC for serial communication)
- Limit switches: 25-pin Sub-D, male Connection option for the built-in limit switches in the robot: 3 axes with 2 limit switches each = 6 sensors Each sensor has 3 pins (+/-/sens) -> 18 pins in total
- Remote control: 26-pin Sub-D, female Connection for a remote control (e.g. buttons directly to the Arduino's digital in pins, display/encoder via I2C)
- Motor X: 4-pin, DIN, male Connection of the X-axis, 2-phase motor used (A+-/B+-)
- Motor Y 4pin, DIN, male Connection of the Y-axis, 2-phase motor used (A+-/B+-)
- Motor Z: 4pin, DIN, male Connection of the Z-axis, 2-phase motor used (A+-/B+-)
- Power: LED with socket In our case, simply connected to the 36V output of the power supply with a series resistor. Indication of whether the power supply is switched on. Could also be used to indicate the power supply to the motor drivers (thus acting as an indicator for the safety circuit consisting of the µC and emergency stop switch)
- Emergency Stop: emergency stop switch that allows the user to immediately disconnect the power to the motor drivers via a relay. In our case, the emergency stop is installed on the remote control. However, it can also be easily integrated into this housing.

### 2.3.4 Back connections

- 230V IEC plug with on/off switch and main fuse (1.75A, slow blow is sufficient).

### 2.3.5 Wiring

Die Verkabelung ist durch die beschrifteten Stecker auf der Platine einfach möglich und sollte kein größeres Problem darstellen.

Das hängt auch sehr davon ab, was alles im Gehäuse verbaut worden ist.

Falls es Fragen gibt meldet euch einfach bei uns

The wire is easily possible through the labeled connectors on the board and should not be a major problem. It also depends on what has been installed in your housing.

If there are any questions, just contact us.

# 3 Software

## 3.1 Arduino / C++

## 3.2 PC / Python

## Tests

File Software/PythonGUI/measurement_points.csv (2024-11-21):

x | y | z
-295.4423259036624 | -3.618124987505693e-14 | -52.09445330007909
-295.4423259036624 | -3.618124987505693e-14 | 52.094453300079124
-295.4423259036624 | 3.618124987505693e-14 | -52.09445330007909
-295.4423259036624 | 3.618124987505693e-14 | 52.094453300079124
-259.8076211353316 | -3.1817257161747206e-14 | -149.99999999999994
-259.8076211353316 | -3.1817257161747206e-14 | 150.00000000000003
-259.8076211353316 | 3.1817257161747206e-14 | -149.99999999999994
-259.8076211353316 | 3.1817257161747206e-14 | 150.00000000000003
-226.32195202064662 | -189.90666646784672 | -52.09445330007909
-226.32195202064662 | -189.90666646784672 | 52.094453300079124
-226.32195202064662 | 189.90666646784672 | -52.09445330007909
-226.32195202064662 | 189.90666646784672 | 52.094453300079124
-199.0241844506815 | -167.00111976792584 | -149.99999999999994
-199.0241844506815 | -167.00111976792584 | 150.00000000000003
-199.0241844506815 | 167.00111976792584 | -149.99999999999994
-199.0241844506815 | 167.00111976792584 | 150.00000000000003
-192.83628290596184 | -2.3615633662025964e-14 | -229.81333293569338
-192.83628290596184 | 2.3615633662025964e-14 | -229.81333293569338
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

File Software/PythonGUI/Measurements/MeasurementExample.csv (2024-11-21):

x | y | z | Bx | By | Bz | Btotal | Average number
310.0 | 263.0 | 390.0 | 0.007732500000000001 | -0.04268319999999999 | -1.6900000000000004e-0 | 0.04319939204883291 | 10.0
310.0 | 263.0 | 395.0 | 0.0079325 | -0.0427832 | 8.31e-05 | 0.043333855425506954 | 10.0
310.0 | 263.0 | 400.0 | 0.008032500000000001 | -0.0427832 | 0.0001831 | 0.043352504372821093 | 10.0
310.0 | 263.0 | 405.0 | 0.008132499999999999 | -0.042883199999999996 | 0.0002831 | 0.04346985506502547 | 10.0
310.0 | 263.0 | 410.0 | 0.008132499999999999 | -0.0429832 | 0.00038310000000000004 | 0.04356891425097234 | 10.0
310.0 | 263.0 | 415.0 | 0.008232499999999998 | -0.0429832 | 0.0004831000000000001 | 0.04358860755388552 | 10.0
310.0 | 263.0 | 420.0 | 0.008232499999999998 | -0.043083199999999995 | 0.0004831000000000001 | 0.04368682697109939 | 10.0
310.0 | 263.0 | 425.0 | 0.0083325 | -0.043083199999999995 | 0.0004831000000000001 | 0.043705668113138176 | 10.0
310.0 | 263.0 | 430.0 | 0.0083325 | -0.043083199999999995 | 0.0005830999999999999 | 0.04370692390109046 | 10.0
310.0 | 263.0 | 435.0 | 0.0083325 | -0.043083199999999995 | 0.0005830999999999999 | 0.04370692390109046 | 10.0
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

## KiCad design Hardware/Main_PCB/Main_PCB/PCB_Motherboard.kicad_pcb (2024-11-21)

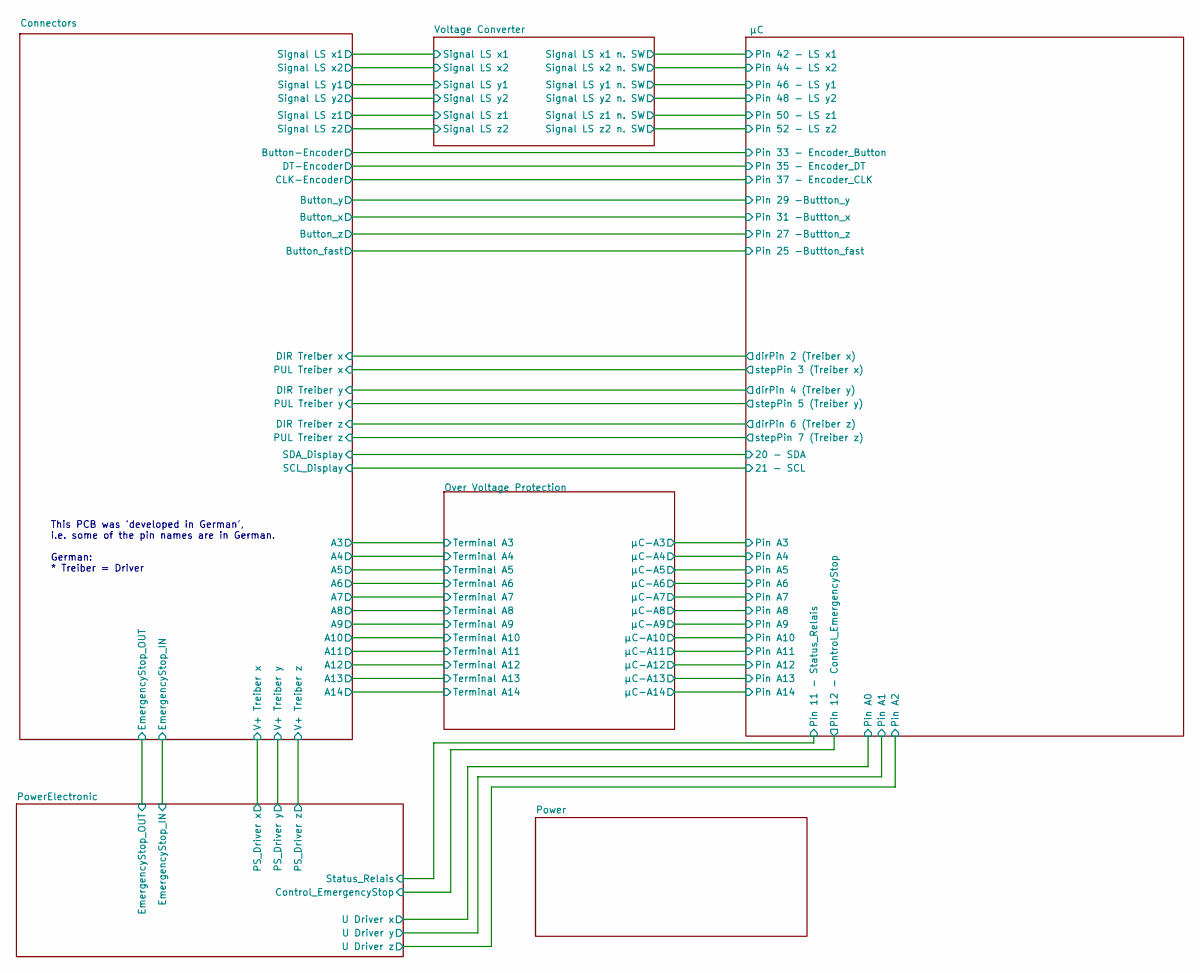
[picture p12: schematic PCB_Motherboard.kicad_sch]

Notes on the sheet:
This PCB was 'developed in German', i.e. some of the pin names are in German. German: * Treiber = Driver

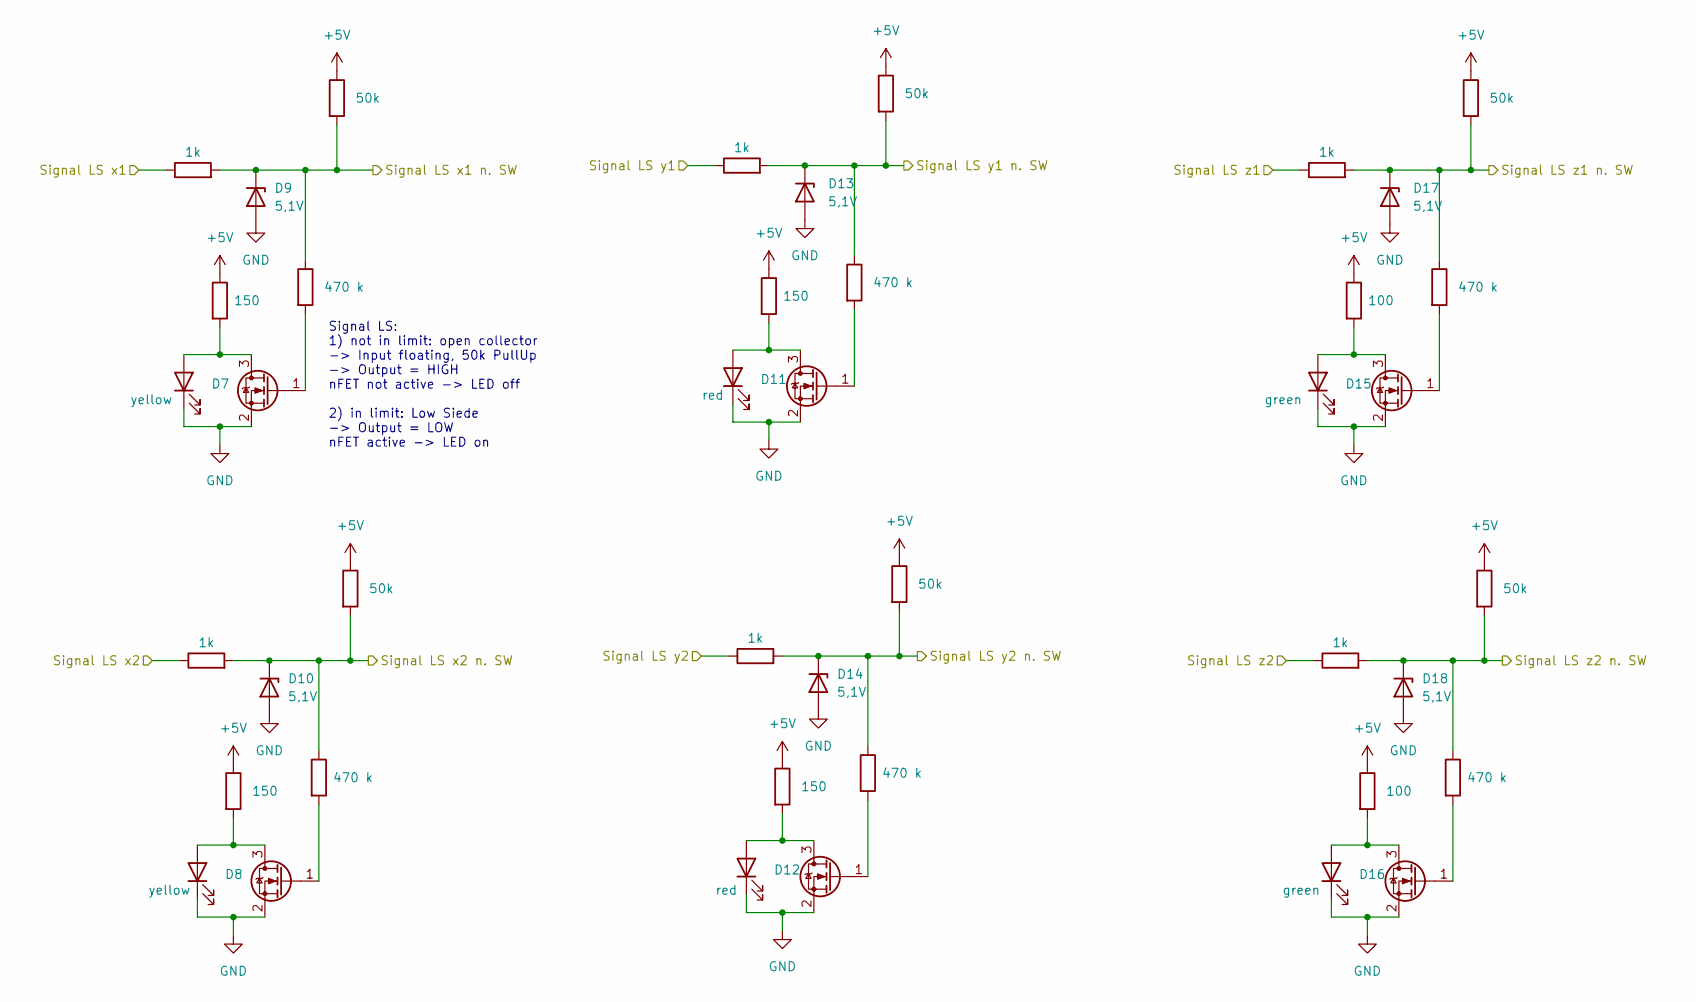
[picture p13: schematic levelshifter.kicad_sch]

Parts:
D7, D8: yellow; LED_0603_1608Metric_Pad1.05x0.95mm_HandSolder
D9, D10, D13, D14, D17, D18: 5,1V; D_SMA_Handsoldering
D11, D12: red; LED_0603_1608Metric_Pad1.05x0.95mm_HandSolder
D15, D16: green; LED_0603_1608Metric_Pad1.05x0.95mm_HandSolder
Q2, Q3, Q4, Q5, Q6, Q7: Q_NMOS_GDS; SOT-23
R14, R15, R22, R23, R30, R31: 1k; R_1206_3216Metric_Pad1.30x1.75mm_HandSolder
R16, R17, R24, R25: 150; R_1206_3216Metric_Pad1.30x1.75mm_HandSolder
R18, R19, R26, R27, R34, R35: 470 k; R_1206_3216Metric_Pad1.30x1.75mm_HandSolder
R20, R21, R28, R29, R36, R37: 50k; R_1206_3216Metric_Pad1.30x1.75mm_HandSolder
R32, R33: 100; R_1206_3216Metric_Pad1.30x1.75mm_HandSolder

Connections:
+5V: R16.1, R17.1, R20.1, R21.1, R24.1, R25.1, R28.1, R29.1, R32.1, R33.1, R36.1, R37.1; also elsewhere on the board
/Connectors/Signal LS x1: R14.1; also elsewhere on the board
/Connectors/Signal LS x2: R15.1; also elsewhere on the board
/Connectors/Signal LS y1: R22.1; also elsewhere on the board
/Connectors/Signal LS y2: R23.1; also elsewhere on the board
/Connectors/Signal LS z1: R30.1; also elsewhere on the board
/Connectors/Signal LS z2: R31.1; also elsewhere on the board
/Voltage Converter/Signal LS x1 n. SW: D9.1 (K), R14.2, R18.1, R20.2; also elsewhere on the board
/Voltage Converter/Signal LS x2 n. SW: D10.1 (K), R15.2, R19.1, R21.2; also elsewhere on the board
/Voltage Converter/Signal LS y1 n. SW: D13.1 (K), R22.2, R26.1, R28.2; also elsewhere on the board
/Voltage Converter/Signal LS y2 n. SW: D14.1 (K), R23.2, R27.1, R29.2; also elsewhere on the board
/Voltage Converter/Signal LS z1 n. SW: D17.1 (K), R30.2, R34.1, R36.2; also elsewhere on the board
/Voltage Converter/Signal LS z2 n. SW: D18.1 (K), R31.2, R35.1, R37.2; also elsewhere on the board
GND: D7.1 (K), D8.1 (K), D9.2 (A), D10.2 (A), D11.1 (K), D12.1 (K), D13.2 (A), D14.2 (A), D15.1 (K), D16.1 (K), D17.2 (A), D18.2 (A), Q2.2 (S), Q3.2 (S), Q4.2 (S), Q5.2 (S), Q6.2 (S), Q7.2 (S); also elsewhere on the board
unnamed: D7.2 (A), Q2.3 (D), R16.2
unnamed: D8.2 (A), Q3.3 (D), R17.2
unnamed: D11.2 (A), Q4.3 (D), R24.2
unnamed: D12.2 (A), Q5.3 (D), R25.2
unnamed: D15.2 (A), Q6.3 (D), R32.2
unnamed: D16.2 (A), Q7.3 (D), R33.2
unnamed: Q2.1 (G), R18.2
unnamed: Q3.1 (G), R19.2
unnamed: Q4.1 (G), R26.2
unnamed: Q5.1 (G), R27.2
unnamed: Q6.1 (G), R34.2
unnamed: Q7.1 (G), R35.2

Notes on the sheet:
Signal LS: 1) not in limit: open collector -> Input floating, 50k PullUp -> Output = HIGH nFET not active -> LED off 2) in limit: Low Siede -> Output = LOW nFET active -> LED on

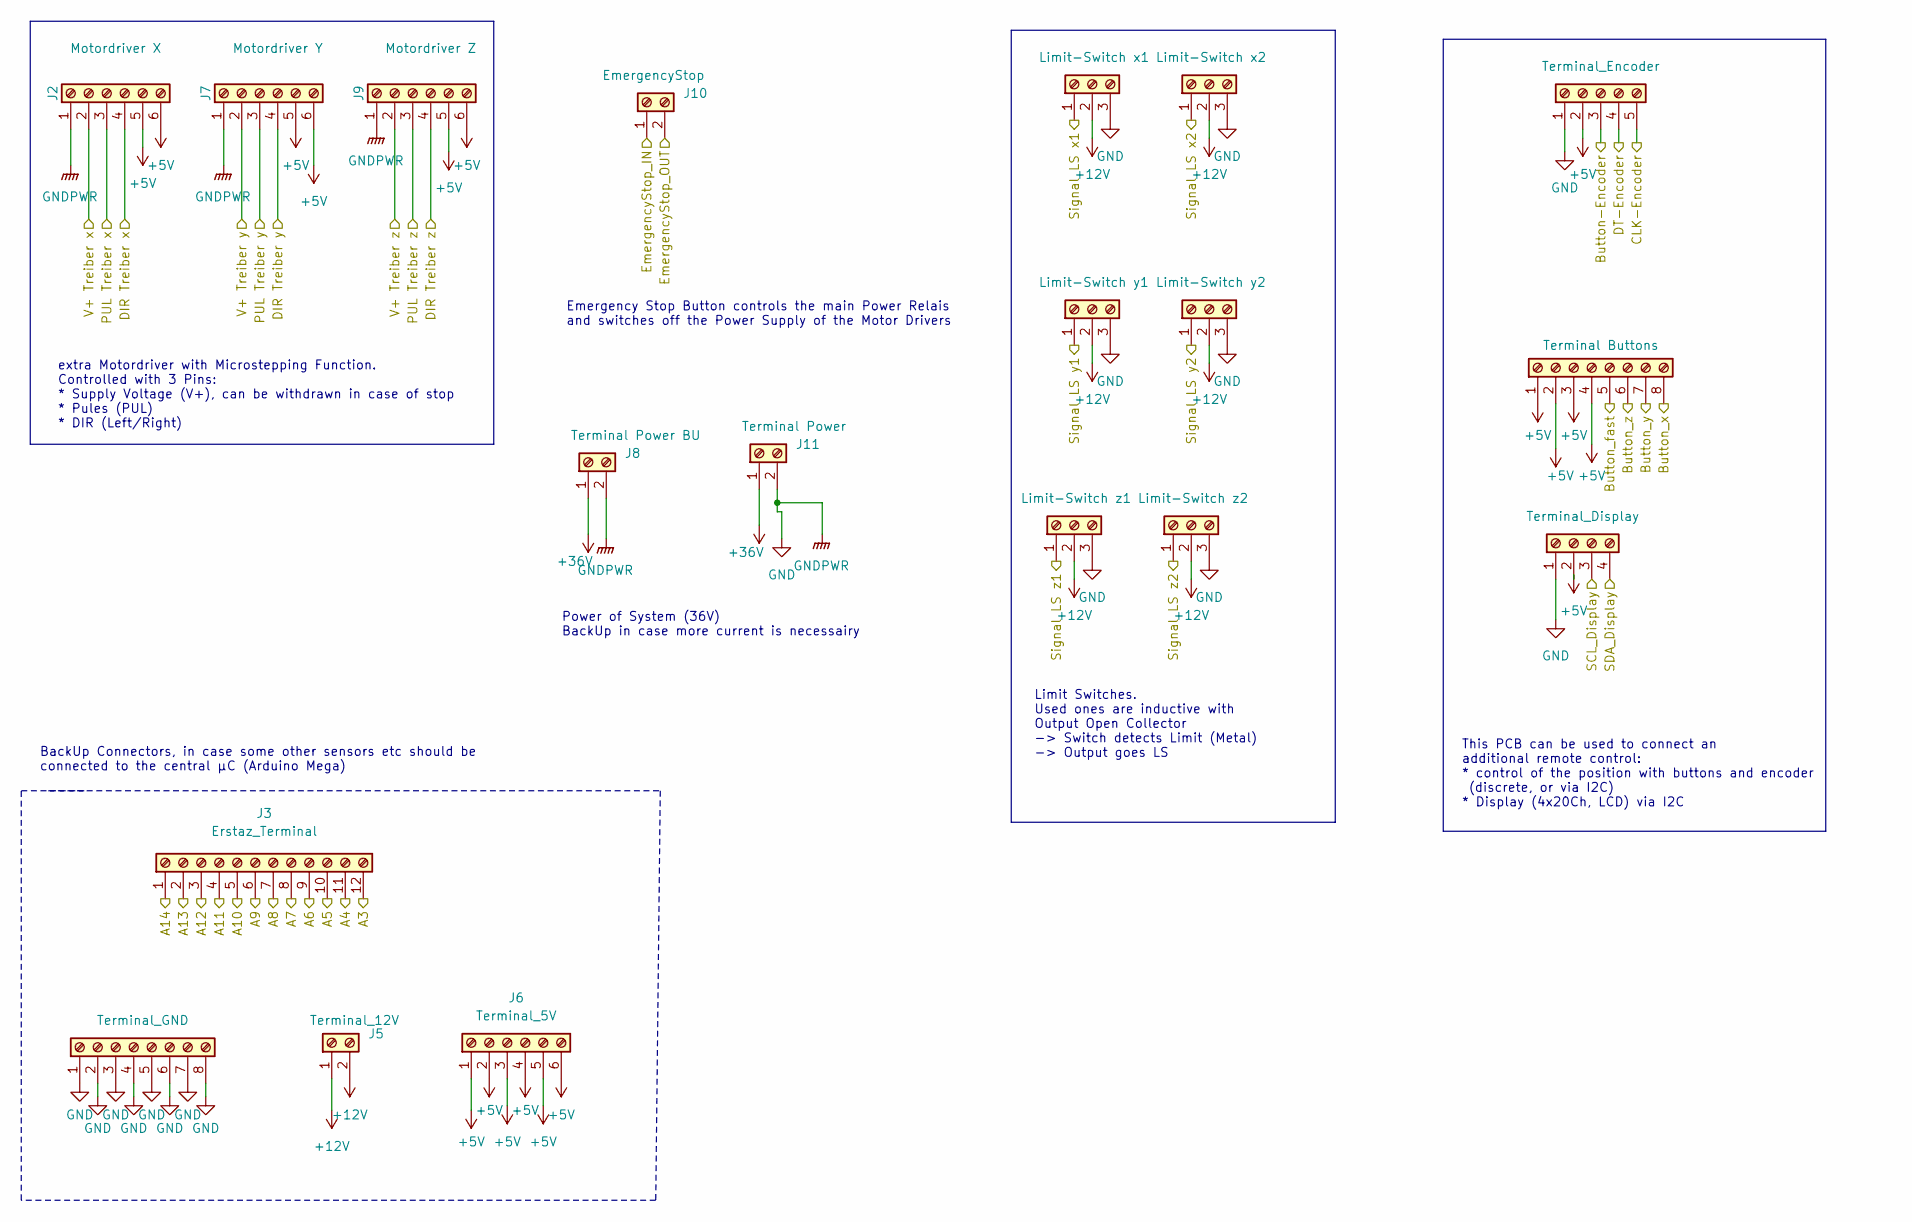
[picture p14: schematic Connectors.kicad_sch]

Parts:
J1: Terminal_Display; PhoenixContact_MC_1,5_4-G-3.81_1x04_P3.81mm_Horizontal
J2: Motordriver X; PhoenixContact_MC_1,5_6-G-3.81_1x06_P3.81mm_Horizontal
J3: Erstaz_Terminal; PhoenixContact_MC_1,5_12-G-3.81_1x12_P3.81mm_Horizontal
J4: Terminal_GND; PhoenixContact_MC_1,5_8-G-3.81_1x08_P3.81mm_Horizontal
J5: Terminal_12V; PhoenixContact_MC_1,5_2-G-3.81_1x02_P3.81mm_Horizontal
J6: Terminal_5V; PhoenixContact_MC_1,5_6-G-3.81_1x06_P3.81mm_Horizontal
J7: Motordriver Y; PhoenixContact_MC_1,5_6-G-3.81_1x06_P3.81mm_Horizontal
J8: Terminal Power BU; PhoenixContact_MC_1,5_2-G-3.81_1x02_P3.81mm_Horizontal
J9: Motordriver Z; PhoenixContact_MC_1,5_6-G-3.81_1x06_P3.81mm_Horizontal
J10: EmergencyStop; PhoenixContact_MC_1,5_2-G-3.81_1x02_P3.81mm_Horizontal
J11: Terminal Power; PhoenixContact_MC_1,5_2-G-3.81_1x02_P3.81mm_Horizontal
J12: Limit-Switch z1; PhoenixContact_MC_1,5_3-G-3.81_1x03_P3.81mm_Horizontal
J13: Limit-Switch x1; PhoenixContact_MC_1,5_3-G-3.81_1x03_P3.81mm_Horizontal
J14: Limit-Switch y1; PhoenixContact_MC_1,5_3-G-3.81_1x03_P3.81mm_Horizontal
J15: Limit-Switch z2; PhoenixContact_MC_1,5_3-G-3.81_1x03_P3.81mm_Horizontal
J16: Limit-Switch x2; PhoenixContact_MC_1,5_3-G-3.81_1x03_P3.81mm_Horizontal
J17: Limit-Switch y2; PhoenixContact_MC_1,5_3-G-3.81_1x03_P3.81mm_Horizontal
J18: Terminal Buttons; PhoenixContact_MC_1,5_8-G-3.81_1x08_P3.81mm_Horizontal
J19: Terminal_Encoder; PhoenixContact_MC_1,5_5-G-3.81_1x05_P3.81mm_Horizontal

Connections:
+5V: J1.2, J2.5, J2.6, J6.1, J6.2, J6.3, J6.4, J6.5, J6.6, J7.5, J7.6, J9.5, J9.6, J18.1, J18.2, J18.3, J18.4, J19.2; also elsewhere on the board
+12V: J5.1, J5.2, J12.2, J13.2, J14.2, J15.2, J16.2, J17.2; also elsewhere on the board
+36V: J8.1, J11.1; also elsewhere on the board
/Connectors/A3: J3.12; also elsewhere on the board
/Connectors/A4: J3.11; also elsewhere on the board
/Connectors/A5: J3.10; also elsewhere on the board
/Connectors/A6: J3.9; also elsewhere on the board
/Connectors/A7: J3.8; also elsewhere on the board
/Connectors/A8: J3.7; also elsewhere on the board
/Connectors/A9: J3.6; also elsewhere on the board
/Connectors/A10: J3.5; also elsewhere on the board
/Connectors/A11: J3.4; also elsewhere on the board
/Connectors/A12: J3.3; also elsewhere on the board
/Connectors/A13: J3.2; also elsewhere on the board
/Connectors/A14: J3.1; also elsewhere on the board
/Connectors/Button-Encoder: J19.3; also elsewhere on the board
/Connectors/Button_fast: J18.5; also elsewhere on the board
/Connectors/Button_x: J18.8; also elsewhere on the board
/Connectors/Button_y: J18.7; also elsewhere on the board
/Connectors/Button_z: J18.6; also elsewhere on the board
/Connectors/CLK-Encoder: J19.5; also elsewhere on the board
/Connectors/DIR Treiber x: J2.4; also elsewhere on the board
/Connectors/DIR Treiber y: J7.4; also elsewhere on the board
/Connectors/DIR Treiber z: J9.4; also elsewhere on the board
/Connectors/DT-Encoder: J19.4; also elsewhere on the board
/Connectors/EmergencyStop_IN: J10.1; also elsewhere on the board
/Connectors/EmergencyStop_OUT: J10.2; also elsewhere on the board
/Connectors/PUL Treiber x: J2.3; also elsewhere on the board
/Connectors/PUL Treiber y: J7.3; also elsewhere on the board
/Connectors/PUL Treiber z: J9.3; also elsewhere on the board
/Connectors/SCL_Display: J1.3; also elsewhere on the board
/Connectors/SDA_Display: J1.4; also elsewhere on the board
/Connectors/Signal LS x1: J13.1; also elsewhere on the board
/Connectors/Signal LS x2: J16.1; also elsewhere on the board
/Connectors/Signal LS y1: J14.1; also elsewhere on the board
/Connectors/Signal LS y2: J17.1; also elsewhere on the board
/Connectors/Signal LS z1: J12.1; also elsewhere on the board
/Connectors/Signal LS z2: J15.1; also elsewhere on the board
/Connectors/V+ Treiber x: J2.2; also elsewhere on the board
/Connectors/V+ Treiber y: J7.2; also elsewhere on the board
/Connectors/V+ Treiber z: J9.2; also elsewhere on the board
GND: J1.1, J2.1, J4.1, J4.2, J4.3, J4.4, J4.5, J4.6, J4.7, J4.8, J7.1, J8.2, J9.1, J11.2, J12.3, J13.3, J14.3, J15.3, J16.3, J17.3, J19.1; also elsewhere on the board

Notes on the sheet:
Power of System (36V) BackUp in case more current is necessairy
Emergency Stop Button controls the main Power Relais and switches off the Power Supply of the Motor Drivers
This PCB can be used to connect an additional remote control: * control of the position with buttons and encoder (discrete, or via I2C) * Display (4x20Ch, LCD) via I2C
extra Motordriver with Microstepping Function. Controlled with 3 Pins: * Supply Voltage (V+), can be withdrawn in case of stop * Pules (PUL) * DIR (Left/Right)
Limit Switches. Used ones are inductive with Output Open Collector -> Switch detects Limit (Metal) -> Output goes LS
BackUp Connectors, in case some other sensors etc should be connected to the central µC (Arduino Mega)

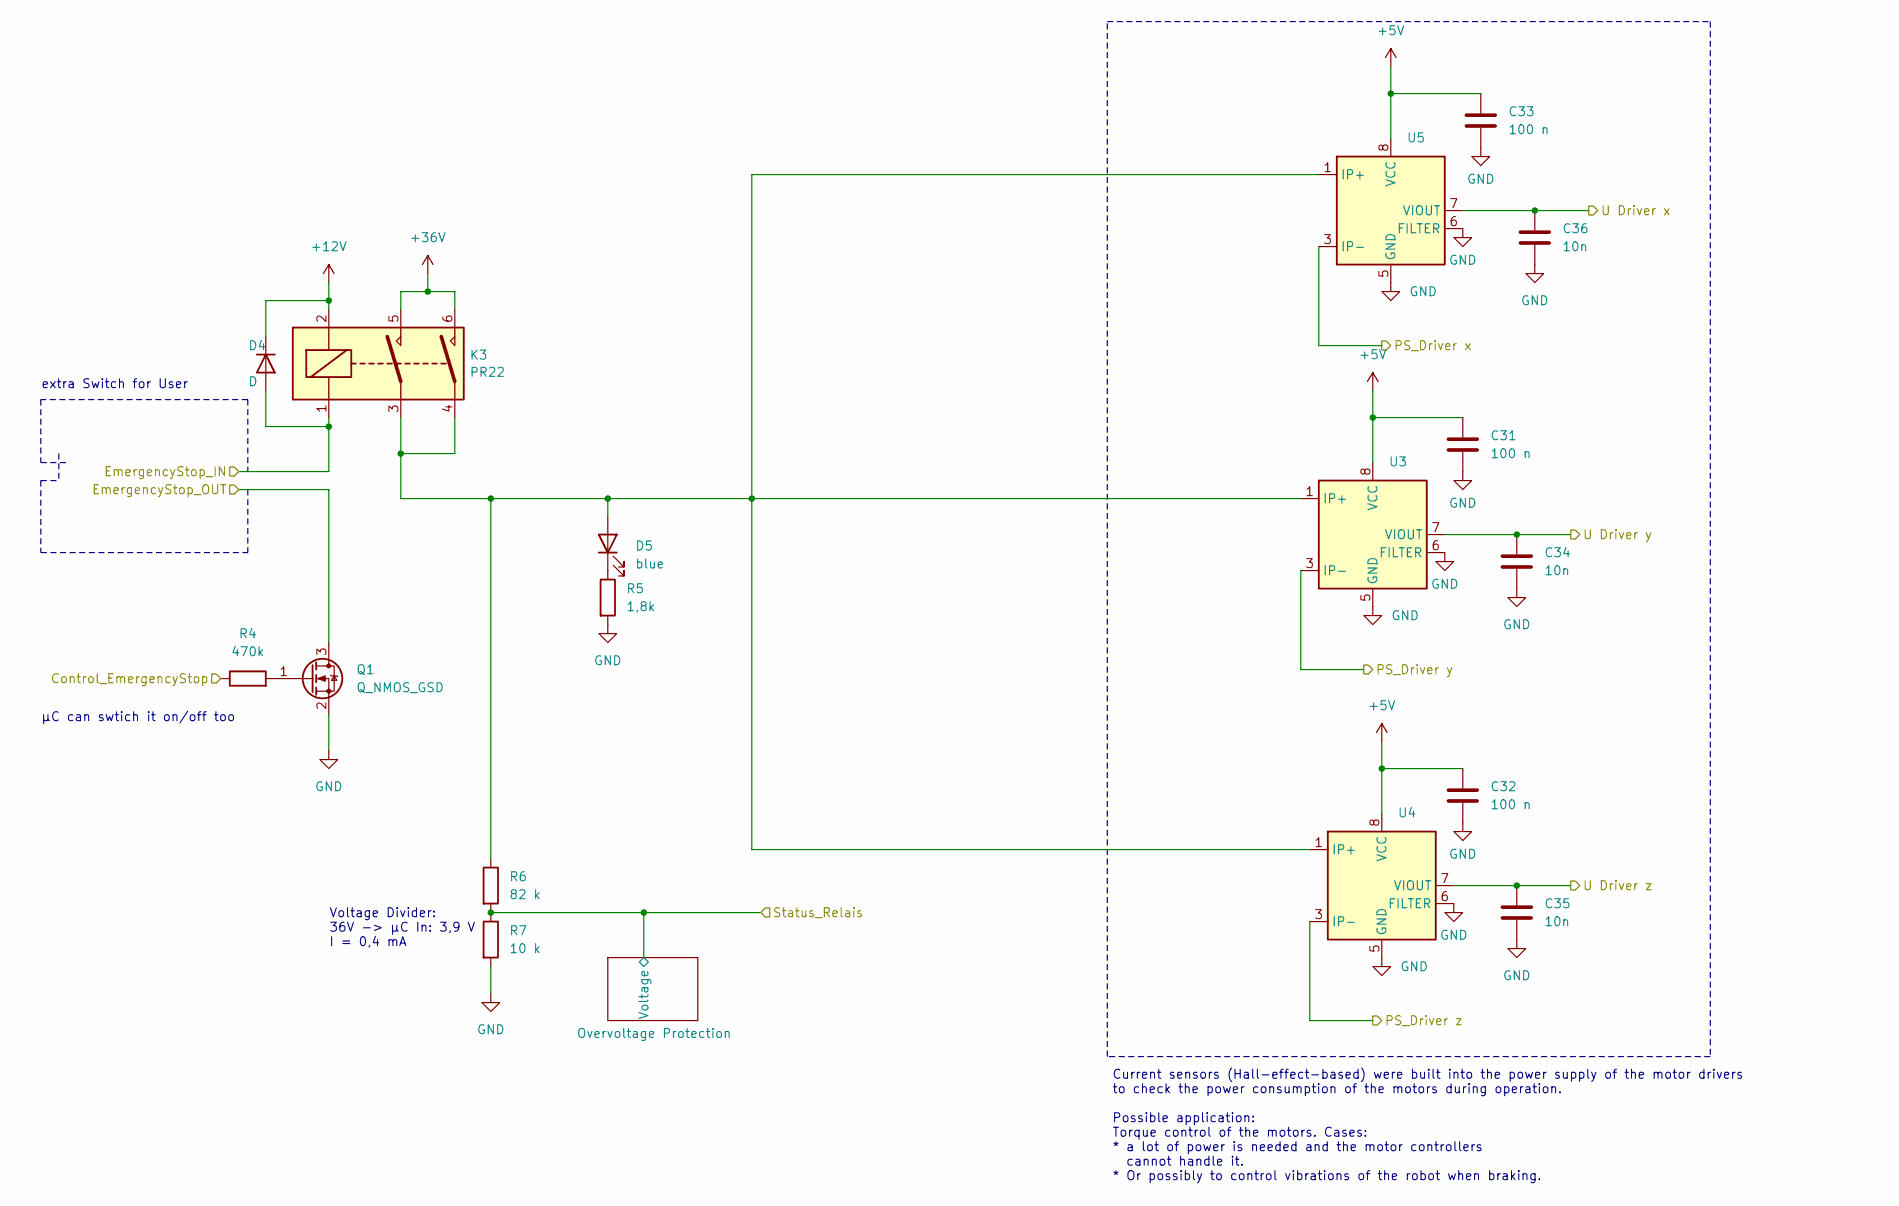
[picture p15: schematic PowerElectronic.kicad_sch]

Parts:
C31, C32, C33: 100 n; C_1206_3216Metric_Pad1.33x1.80mm_HandSolder
C34, C35, C36: 10n; C_1206_3216Metric_Pad1.33x1.80mm_HandSolder
D4: D; D_1206_3216Metric_Pad1.42x1.75mm_HandSolder
D5: blue; LED_0603_1608Metric_Pad1.05x0.95mm_HandSolder
K3: PR22; Relay_PR22
Q1: Q_NMOS_GSD; SOT-23
R4: 470k; R_1206_3216Metric_Pad1.30x1.75mm_HandSolder
R5: 1,8k; R_1206_3216Metric_Pad1.30x1.75mm_HandSolder
R6: 82 k; R_1206_3216Metric_Pad1.30x1.75mm_HandSolder
R7: 10 k; R_1206_3216Metric_Pad1.30x1.75mm_HandSolder
U3, U4, U5: SOIC-8_3.9x4.9mm_P1.27mm

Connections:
+5V: C31.1, C32.1, C33.1, U3.8 (VCC), U4.8 (VCC), U5.8 (VCC); also elsewhere on the board
+12V: D4.1 (K), K3.2; also elsewhere on the board
+36V: K3.5, K3.6; also elsewhere on the board
/Connectors/EmergencyStop_IN: D4.2 (A), K3.1; also elsewhere on the board
/Connectors/EmergencyStop_OUT: Q1.3 (D); also elsewhere on the board
/Connectors/V+ Treiber x: U5.3 (IP-), U5.4 (IP-); also elsewhere on the board
/Connectors/V+ Treiber y: U3.3 (IP-), U3.4 (IP-); also elsewhere on the board
/Connectors/V+ Treiber z: U4.3 (IP-), U4.4 (IP-); also elsewhere on the board
/PowerElectronic/Control_EmergencyStop: R4.1; also elsewhere on the board
/PowerElectronic/Status_Relais: R6.2, R7.1; also elsewhere on the board
/PowerElectronic/U Driver x: C36.1, U5.7 (VIOUT); also elsewhere on the board
/PowerElectronic/U Driver y: C34.1, U3.7 (VIOUT); also elsewhere on the board
/PowerElectronic/U Driver z: C35.1, U4.7 (VIOUT); also elsewhere on the board
GND: C31.2, C32.2, C33.2, C34.2, C35.2, C36.2, Q1.2 (S), R5.2, R7.2, U3.5 (GND), U3.6 (FILTER), U4.5 (GND), U4.6 (FILTER), U5.5 (GND), U5.6 (FILTER); also elsewhere on the board
unnamed: D5.2 (A), K3.3, K3.4, R6.1, U3.1 (IP+), U3.2 (IP+), U4.1 (IP+), U4.2 (IP+), U5.1 (IP+), U5.2 (IP+)
unnamed: D5.1 (K), R5.1
unnamed: Q1.1 (G), R4.2

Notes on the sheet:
Current sensors (Hall-effect-based) were built into the power supply of the motor drivers to check the power consumption of the motors during operation. Possible application: Torque control of the motors. Cases: * a lot of power is needed and the motor controllers cannot handle it. * Or possibly to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
Voltage Divider: 36V -> µC In: 3,9 V I = 0,4 mA
µC can swtich it on/off too
extra Switch for User

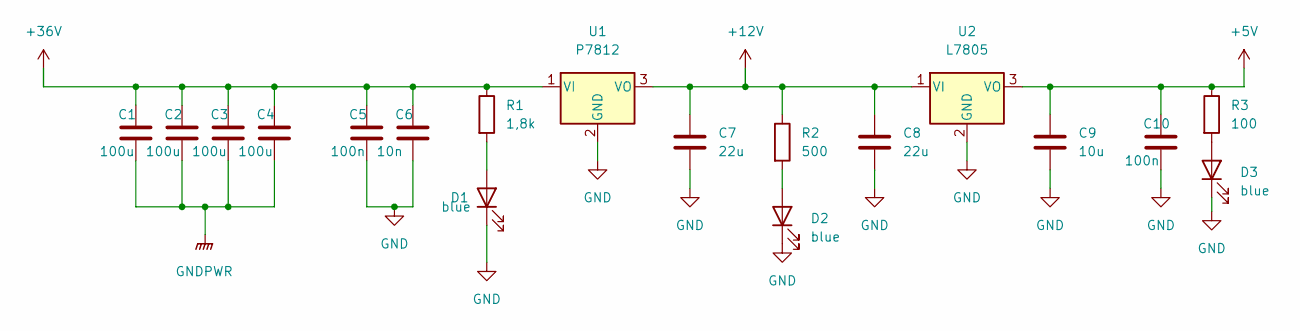
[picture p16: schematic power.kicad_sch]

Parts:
C1, C2, C3, C4: 100u; CP_Elec_8x6.2
C5, C10: 100n; C_1206_3216Metric_Pad1.33x1.80mm_HandSolder
C6: 10n; C_1206_3216Metric_Pad1.33x1.80mm_HandSolder
C7, C8: 22u; C_1206_3216Metric_Pad1.33x1.80mm_HandSolder
C9: 10u; C_1206_3216Metric_Pad1.33x1.80mm_HandSolder
D1, D2, D3: blue; LED_0603_1608Metric_Pad1.05x0.95mm_HandSolder
R1: 1,8k; R_1206_3216Metric_Pad1.30x1.75mm_HandSolder
R2: 500; R_1206_3216Metric_Pad1.30x1.75mm_HandSolder
R3: 100; R_1206_3216Metric_Pad1.30x1.75mm_HandSolder
U1: P7812
U2: L7805; P7812

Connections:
+5V: C9.1, C10.1, R3.1, U2.3 (VO); also elsewhere on the board
+12V: C7.1, C8.1, R2.1, U1.3 (VO), U2.1 (VI); also elsewhere on the board
+36V: C1.1, C2.1, C3.1, C4.1, C5.1, C6.1, R1.1, U1.1 (VI); also elsewhere on the board
GND: C1.2, C2.2, C3.2, C4.2, C5.2, C6.2, C7.2, C8.2, C9.2, C10.2, D1.1 (K), D2.1 (K), D3.1 (K), U1.2 (GND), U2.2 (GND); also elsewhere on the board
unnamed: D1.2 (A), R1.2
unnamed: D2.2 (A), R2.2
unnamed: D3.2 (A), R3.2

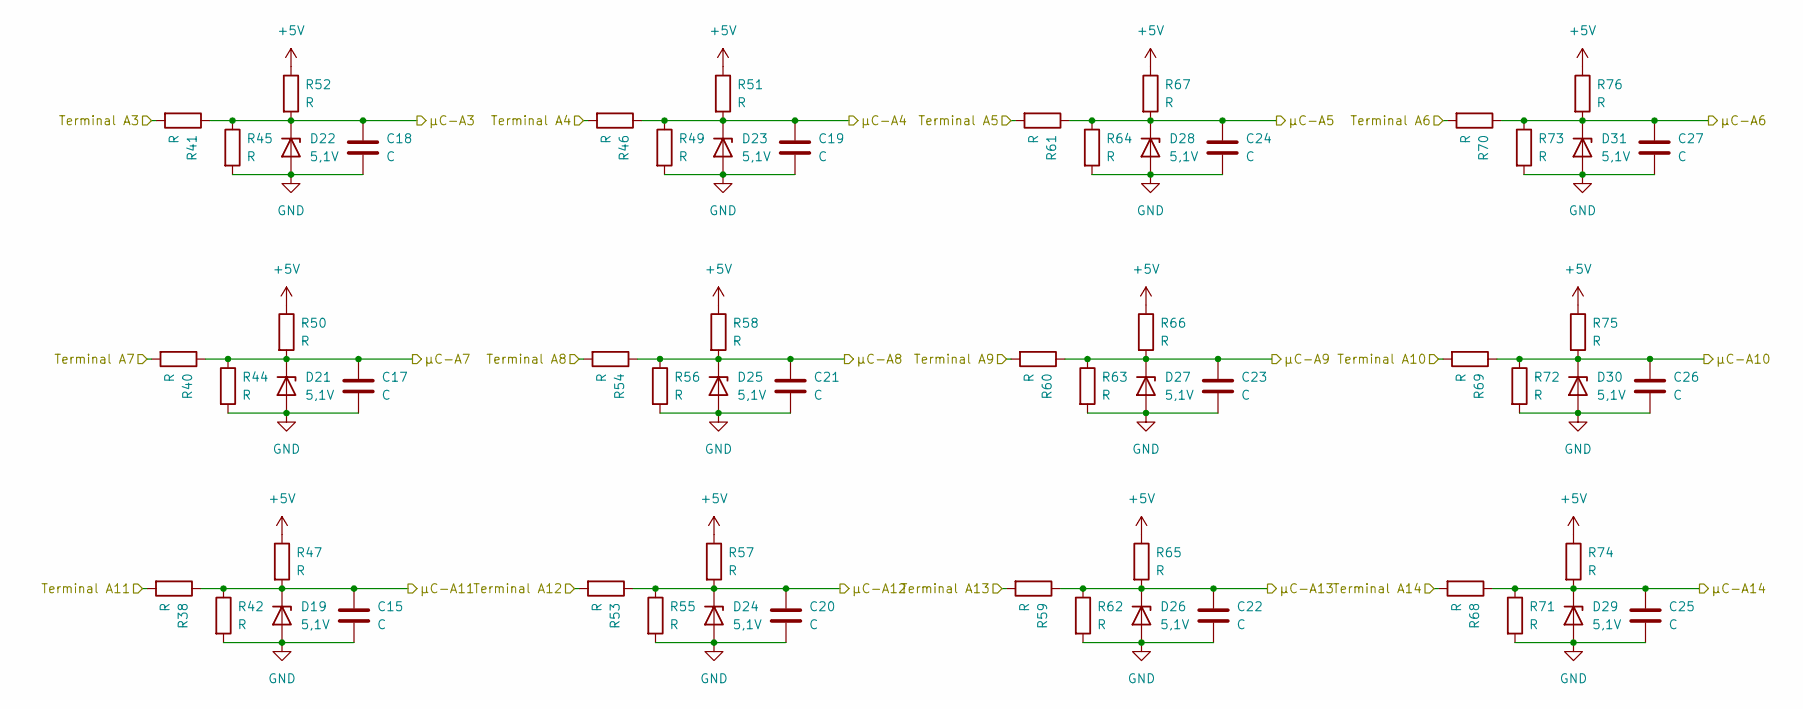
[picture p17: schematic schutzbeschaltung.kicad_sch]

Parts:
C15, C17, C18, C19, C20, C21, C22, C23, C24, C25, C26, C27: C; C_1206_3216Metric_Pad1.33x1.80mm_HandSolder
D19, D21, D22, D23, D24, D25, D26, D27, D28, D29, D30, D31: 5,1V; D_SMA_Handsoldering
R38, R40, R41, R42, R44, R45, R46, R47, R49, R50, R51, R52, R53, R54, R55, R56, R57, R58, R59, R60, R61, R62, R63, R64, R65, R66, R67, R68, R69, R70, R71, R72, R73, R74, R75, R76: R; R_1206_3216Metric_Pad1.30x1.75mm_HandSolder

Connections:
+5V: R47.1, R50.1, R51.1, R52.1, R57.1, R58.1, R65.1, R66.1, R67.1, R74.1, R75.1, R76.1; also elsewhere on the board
/Connectors/A3: R41.2; also elsewhere on the board
/Connectors/A4: R46.2; also elsewhere on the board
/Connectors/A5: R61.2; also elsewhere on the board
/Connectors/A6: R70.2; also elsewhere on the board
/Connectors/A7: R40.2; also elsewhere on the board
/Connectors/A8: R54.2; also elsewhere on the board
/Connectors/A9: R60.2; also elsewhere on the board
/Connectors/A10: R69.2; also elsewhere on the board
/Connectors/A11: R38.2; also elsewhere on the board
/Connectors/A12: R53.2; also elsewhere on the board
/Connectors/A13: R59.2; also elsewhere on the board
/Connectors/A14: R68.2; also elsewhere on the board
/Over Voltage Protection/µC-A3: C18.1, D22.1 (K), R41.1, R45.1, R52.2; also elsewhere on the board
/Over Voltage Protection/µC-A4: C19.1, D23.1 (K), R46.1, R49.1, R51.2; also elsewhere on the board
/Over Voltage Protection/µC-A5: C24.1, D28.1 (K), R61.1, R64.1, R67.2; also elsewhere on the board
/Over Voltage Protection/µC-A6: C27.1, D31.1 (K), R70.1, R73.1, R76.2; also elsewhere on the board
/Over Voltage Protection/µC-A7: C17.1, D21.1 (K), R40.1, R44.1, R50.2; also elsewhere on the board
/Over Voltage Protection/µC-A8: C21.1, D25.1 (K), R54.1, R56.1, R58.2; also elsewhere on the board
/Over Voltage Protection/µC-A9: C23.1, D27.1 (K), R60.1, R63.1, R66.2; also elsewhere on the board
/Over Voltage Protection/µC-A10: C26.1, D30.1 (K), R69.1, R72.1, R75.2; also elsewhere on the board
/Over Voltage Protection/µC-A11: C15.1, D19.1 (K), R38.1, R42.1, R47.2; also elsewhere on the board
/Over Voltage Protection/µC-A12: C20.1, D24.1 (K), R53.1, R55.1, R57.2; also elsewhere on the board
/Over Voltage Protection/µC-A13: C22.1, D26.1 (K), R59.1, R62.1, R65.2; also elsewhere on the board
/Over Voltage Protection/µC-A14: C25.1, D29.1 (K), R68.1, R71.1, R74.2; also elsewhere on the board
GND: C15.2, C17.2, C18.2, C19.2, C20.2, C21.2, C22.2, C23.2, C24.2, C25.2, C26.2, C27.2, D19.2 (A), D21.2 (A), D22.2 (A), D23.2 (A), D24.2 (A), D25.2 (A), D26.2 (A), D27.2 (A), D28.2 (A), D29.2 (A), D30.2 (A), D31.2 (A), R42.2, R44.2, R45.2, R49.2, R55.2, R56.2, R62.2, R63.2, R64.2, R71.2, R72.2, R73.2; also elsewhere on the board

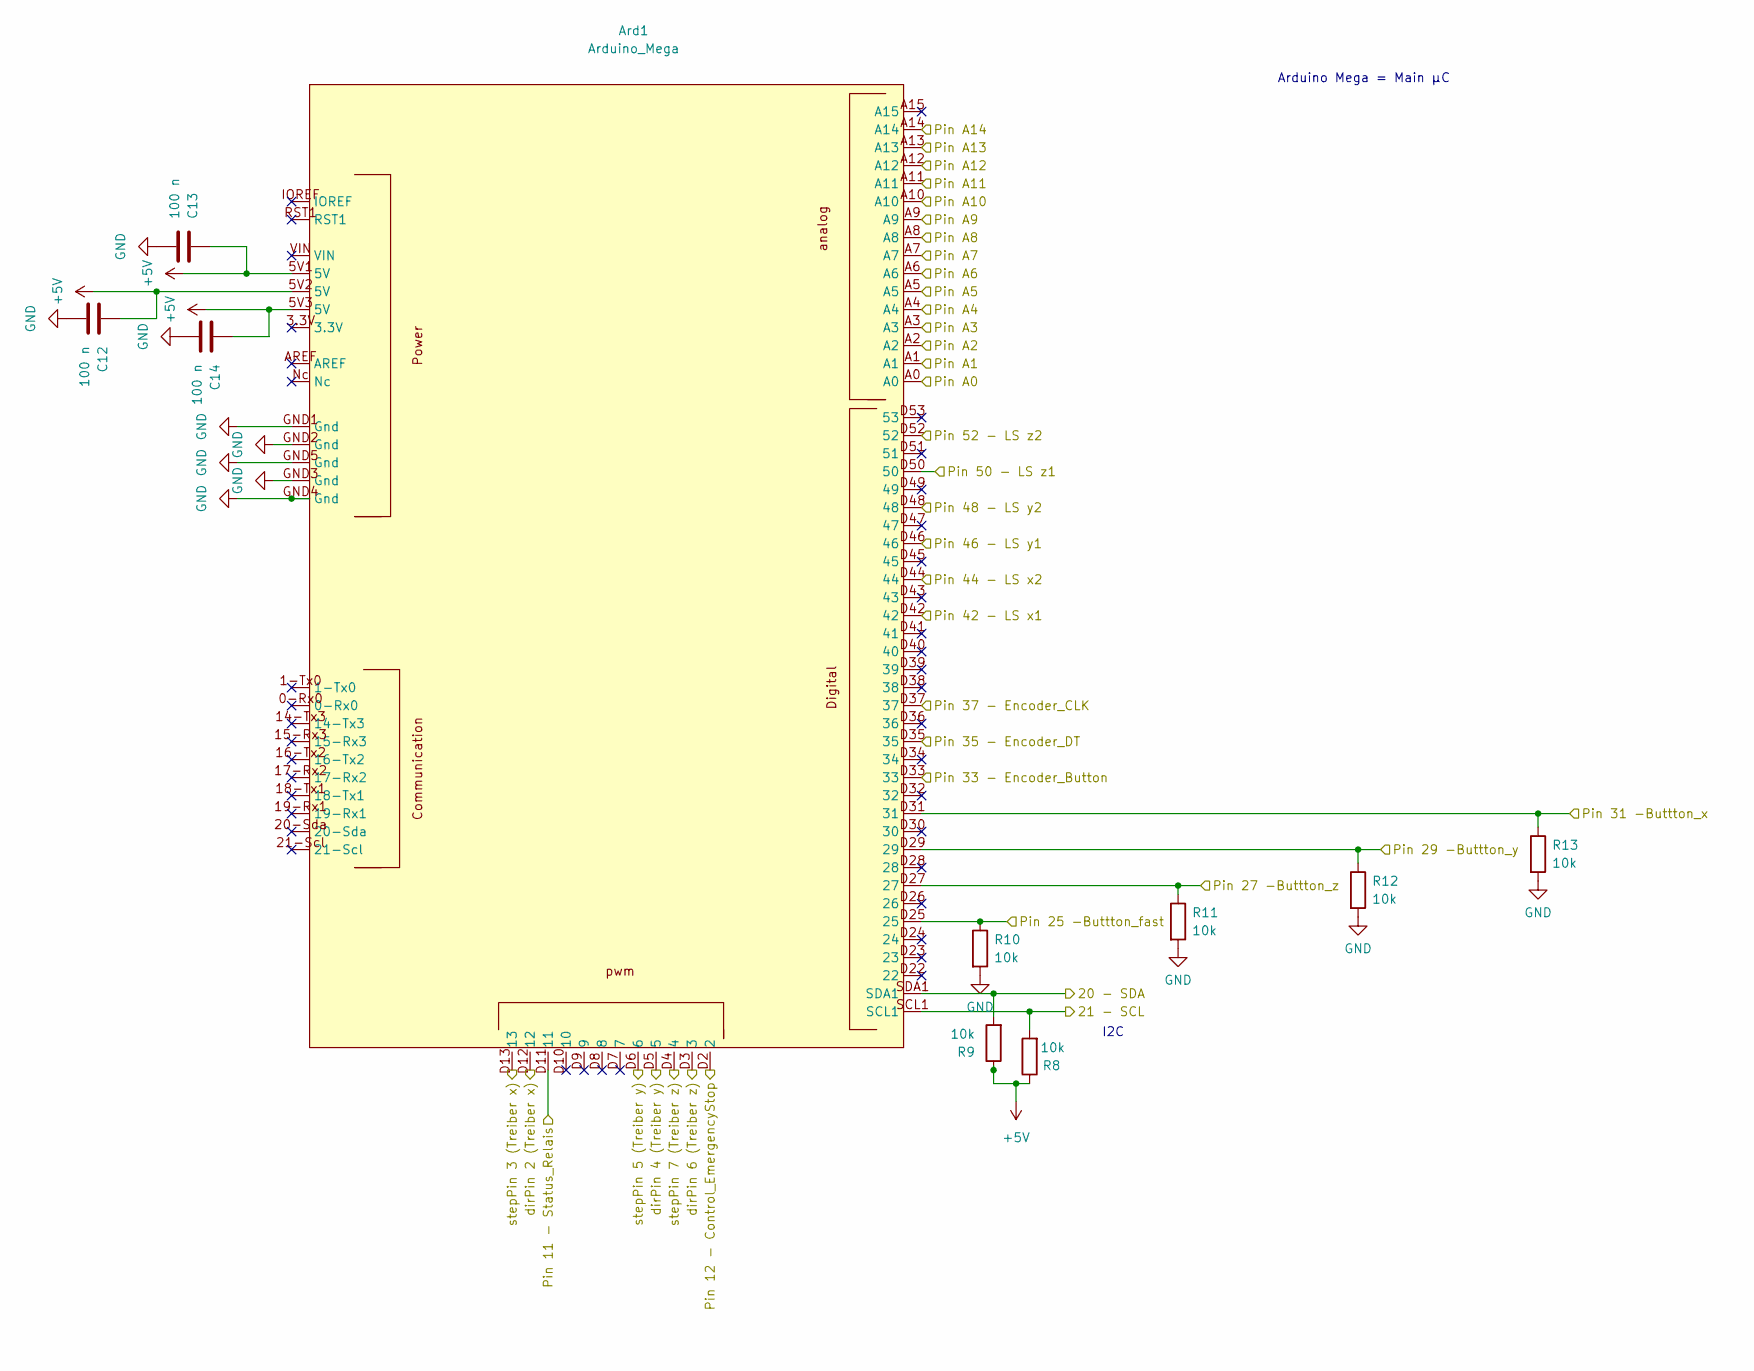
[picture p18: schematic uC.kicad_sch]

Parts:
Ard1: Arduino_Mega; Arduino-Mega
C12, C13, C14: 100 n; C_1206_3216Metric_Pad1.33x1.80mm_HandSolder
R8, R9, R10, R11, R12, R13: 10k; R_1206_3216Metric_Pad1.30x1.75mm_HandSolder

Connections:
+5V: Ard1.5V1 (5V), Ard1.5V2 (5V), Ard1.5V3 (5V), C12.1, C13.1, C14.1, R8.1, R9.1; also elsewhere on the board
/Connectors/Button-Encoder: Ard1.D33 (33); also elsewhere on the board
/Connectors/Button_fast: Ard1.D25 (25), R10.1; also elsewhere on the board
/Connectors/Button_x: Ard1.D31 (31), R13.1; also elsewhere on the board
/Connectors/Button_y: Ard1.D29 (29), R12.1; also elsewhere on the board
/Connectors/Button_z: Ard1.D27 (27), R11.1; also elsewhere on the board
/Connectors/CLK-Encoder: Ard1.D37 (37); also elsewhere on the board
/Connectors/DIR Treiber x: Ard1.D12 (12); also elsewhere on the board
/Connectors/DIR Treiber y: Ard1.D5 (5); also elsewhere on the board
/Connectors/DIR Treiber z: Ard1.D3 (3); also elsewhere on the board
/Connectors/DT-Encoder: Ard1.D35 (35); also elsewhere on the board
/Connectors/PUL Treiber x: Ard1.D13 (13); also elsewhere on the board
/Connectors/PUL Treiber y: Ard1.D6 (6); also elsewhere on the board
/Connectors/PUL Treiber z: Ard1.D4 (4); also elsewhere on the board
/Connectors/SCL_Display: Ard1.SCL1, R8.2; also elsewhere on the board
/Connectors/SDA_Display: Ard1.SDA1, R9.2; also elsewhere on the board
/Over Voltage Protection/µC-A3: Ard1.A3; also elsewhere on the board
/Over Voltage Protection/µC-A4: Ard1.A4; also elsewhere on the board
/Over Voltage Protection/µC-A5: Ard1.A5; also elsewhere on the board
/Over Voltage Protection/µC-A6: Ard1.A6; also elsewhere on the board
/Over Voltage Protection/µC-A7: Ard1.A7; also elsewhere on the board
/Over Voltage Protection/µC-A8: Ard1.A8; also elsewhere on the board
/Over Voltage Protection/µC-A9: Ard1.A9; also elsewhere on the board
/Over Voltage Protection/µC-A10: Ard1.A10; also elsewhere on the board
/Over Voltage Protection/µC-A11: Ard1.A11; also elsewhere on the board
/Over Voltage Protection/µC-A12: Ard1.A12; also elsewhere on the board
/Over Voltage Protection/µC-A13: Ard1.A13; also elsewhere on the board
/Over Voltage Protection/µC-A14: Ard1.A14; also elsewhere on the board
/PowerElectronic/Control_EmergencyStop: Ard1.D2 (2); also elsewhere on the board
/PowerElectronic/Status_Relais: Ard1.D11 (11); also elsewhere on the board
/PowerElectronic/U Driver x: Ard1.A0; also elsewhere on the board
/PowerElectronic/U Driver y: Ard1.A1; also elsewhere on the board
/PowerElectronic/U Driver z: Ard1.A2; also elsewhere on the board
/Voltage Converter/Signal LS x1 n. SW: Ard1.D42 (42); also elsewhere on the board
/Voltage Converter/Signal LS x2 n. SW: Ard1.D44 (44); also elsewhere on the board
/Voltage Converter/Signal LS y1 n. SW: Ard1.D46 (46); also elsewhere on the board
/Voltage Converter/Signal LS y2 n. SW: Ard1.D48 (48); also elsewhere on the board
/Voltage Converter/Signal LS z1 n. SW: Ard1.D50 (50); also elsewhere on the board
/Voltage Converter/Signal LS z2 n. SW: Ard1.D52 (52); also elsewhere on the board
GND: Ard1.GND1 (Gnd), Ard1.GND2 (Gnd), Ard1.GND3 (Gnd), Ard1.GND4 (Gnd), Ard1.GND5 (Gnd), C12.2, C13.2, C14.2, R10.2, R11.2, R12.2, R13.2; also elsewhere on the board

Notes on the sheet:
Arduino Mega = Main µC
I2C

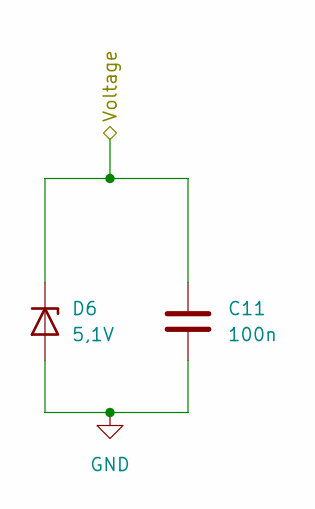
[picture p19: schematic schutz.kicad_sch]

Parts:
C11: 100n; C_1206_3216Metric_Pad1.33x1.80mm_HandSolder
D6: 5,1V; D_SMA_Handsoldering

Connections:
/PowerElectronic/Status_Relais: C11.1, D6.1 (K); also elsewhere on the board
GND: C11.2, D6.2 (A); also elsewhere on the board

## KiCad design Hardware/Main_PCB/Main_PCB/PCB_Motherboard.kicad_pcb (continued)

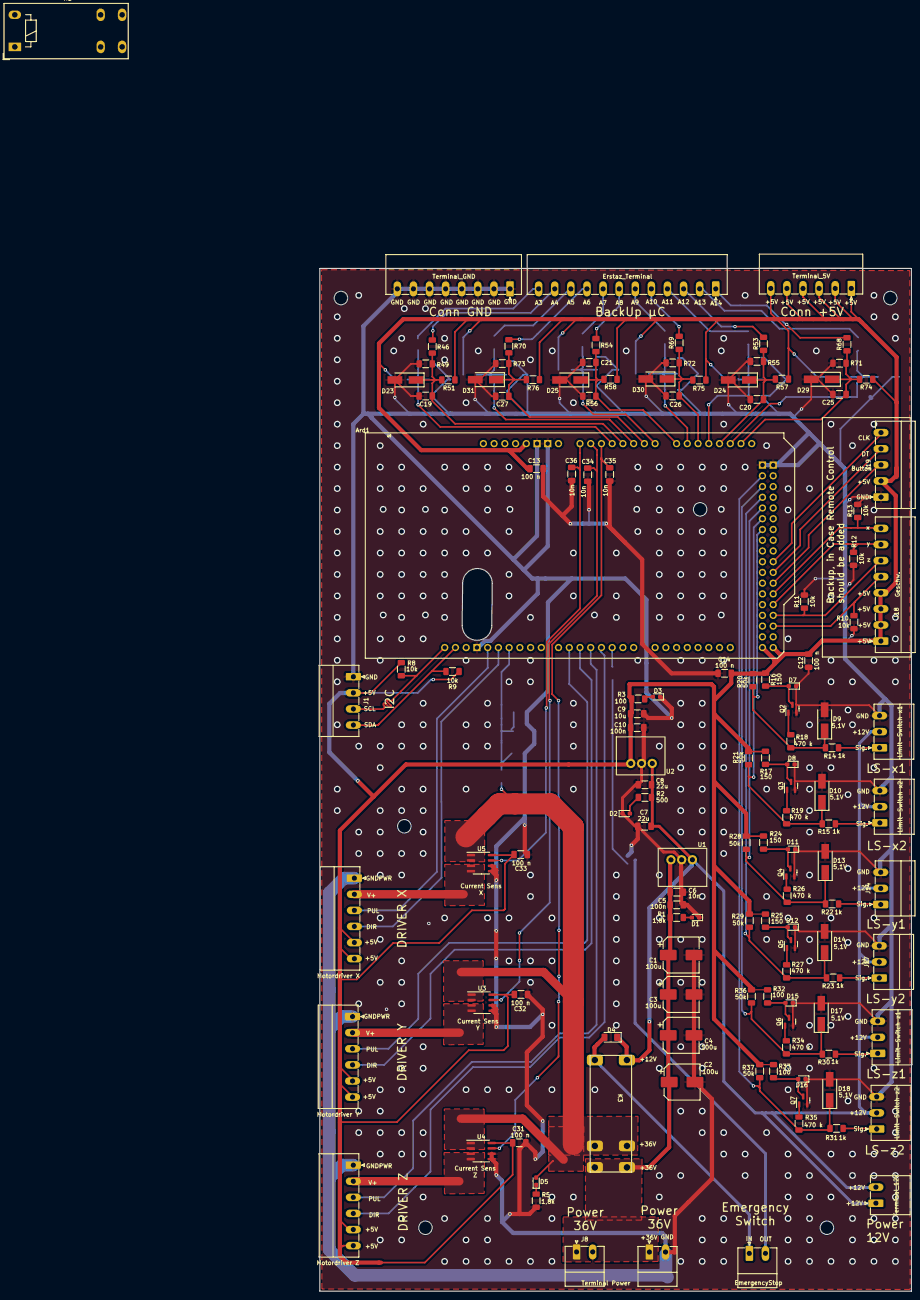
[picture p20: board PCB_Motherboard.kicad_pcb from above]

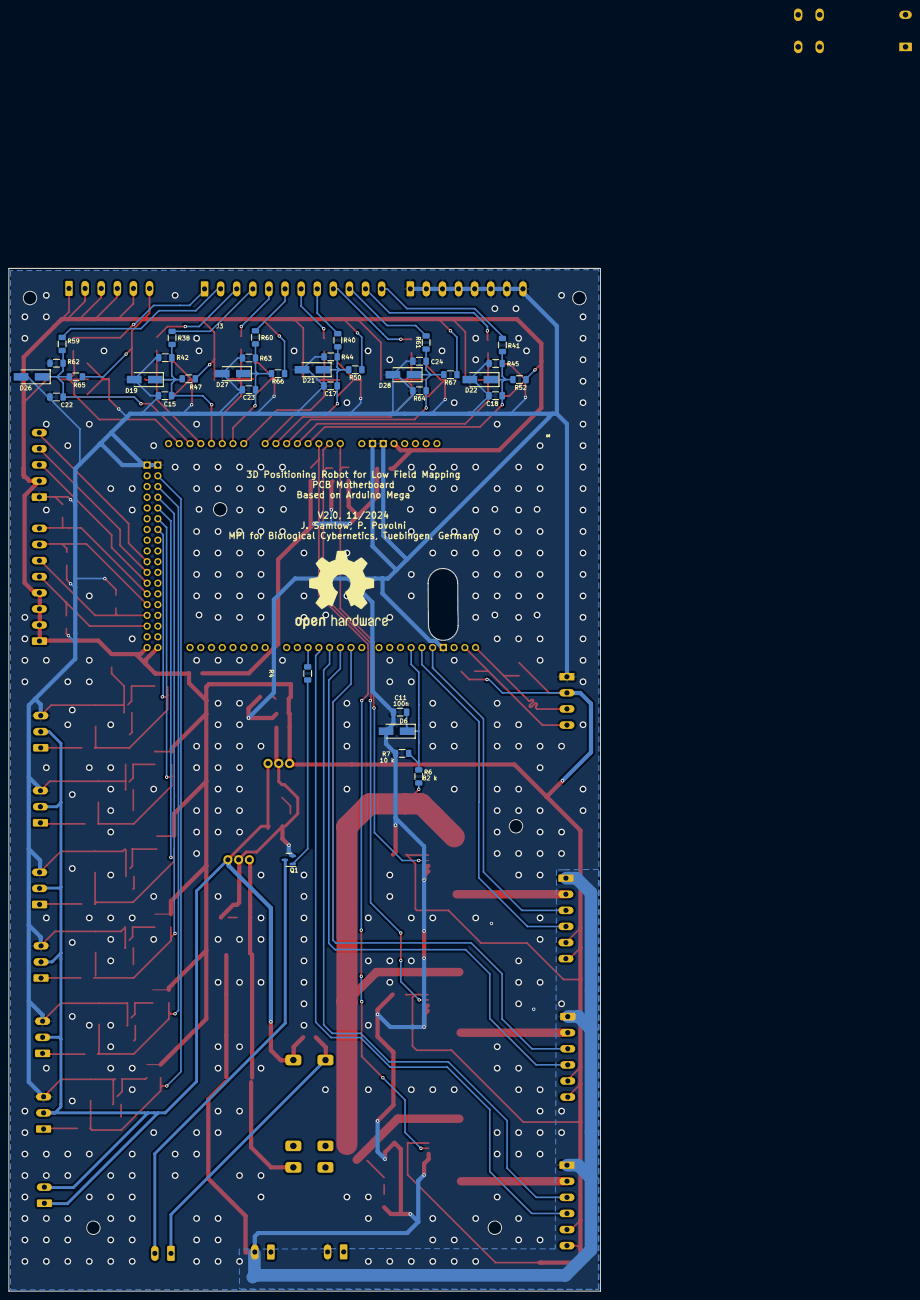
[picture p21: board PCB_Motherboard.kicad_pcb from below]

Board: 2 copper layers, 140.0 x 242.0 mm, 175 parts (37 on the bottom side), 83 nets.

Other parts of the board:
 : MountingHole_3.2mm_M3_DIN965
 #2,  #3,  #4,  #5,  #6: MountingHole_3.2mm_M3_DIN965
K1: PR22-12V-400-1A; Relay_SPST_Schrack-RT1-16A-FormA_RM5mm

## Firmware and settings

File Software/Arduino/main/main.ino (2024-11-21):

#include <AccelStepper.h>


//Variablen für die Taster
struct Pins_str {

  //Taster Konsole
  uint8_t Sw_x;  //x-Achse
  uint8_t Sw_y;  //y-Achse
  uint8_t Sw_z;  //z
  uint8_t Sw_v;  //Speed Auswahl
  uint8_t Sw_Extra;

  //Endschalter
  uint8_t LS_y1;  //x1
  uint8_t LS_y2;
  uint8_t LS_x1;
  uint8_t LS_x2;
  uint8_t LS_z1;
  uint8_t LS_z2;

  //Notaus
  uint8_t Sw_Notaus;   //Abfrage, wie der Zustand phys Notschalter ist
  uint8_t Set_Notaus;  // Schalte den Notaus ein
};

Pins_str Pins = {
  31,   //Sw_x;
  29,   //Sw_y
  27,   //Sw_z
  25,   //Sw_v
  A10,  //Sw_Extra
  42,   //LS_x1
  44,   //LS_x2
  46,   //LS_y1
  48,   //LS_y2
  50,   //LS_z1
  52,   //LS_z2
  11,   //Sw_Notaus
  2     //Set_Notaus
};



// Definition Schrittmotoren
AccelStepper stepperX(AccelStepper::DRIVER, 13, 12);
AccelStepper stepperY(AccelStepper::DRIVER, 6, 5);
AccelStepper stepperZ(AccelStepper::DRIVER, 4, 3);



//Endschalter Struct
struct LS_str {
  bool one;  // true wenn einer der Schalter aktiv
  bool x1;
  bool x2;
  bool y1;
  bool y2;
  bool z1;
  bool z2;
};

LS_str LS = {
  false,
  false,
  false,
  false,
  false,
  false,
  false
};

//Status Struct in Schritten
struct Status_str {  //Roboterkoordinaten
  long posX;
  long posY;
  long posZ;
  bool Error;  // Error während der Messung, aber nicht gefählrich (zB LS sind getriggert, obwohl das nicht sein sollte)

  bool Notaus;  // Muss gemessen werden. Sicherer Zustand = true (Notaus ist getriggert)
};

Status_str Status = {
  0,
  0,
  0,
  false,
  true
};

//Messeinstellungen Struct
struct Config_str {  //pins
  long lengthX; // In R-Steps
  long lengthY;
  long lengthZ;

  double minres_stepper;  //Kleinste Auflösung des Schrittmotors in mm  = SStep 1 (10mm/1600) -> Falsche Spindelmutter geliefert, daher 10mm Steigung... (oder so ähnlich)  
  double minres_roboter;  //Kleinste Auflösung des Roboters in mm  = RStep 1. minres_roboter = minres_stepper * steps_perminres
  long steps_perminres;   // Wähle Mindestschrittweite im Roboter KoorSystem (ca 0,1mm <=> 16 Schritte)
  long steps_perrev;      //
  long zgain;             // z Achse Gain, weil doppelte Steigung verbaut
};

Config_str Config = {
  6630,  // 106.080 -> 6630 R-Steps (16Steps pro 0.1mm)
  6060,  //96.960 -> 6060 R-Steps (bei 16 Steps pro 0.1mm)
  6870,  // Mit aktueller Konfig macht die z-Achse maximal 219.840 Schritte, Steigung 5mm -> 0.1mm=32S -> max_l = 6870 
  0.00625,  
  0.1,
  16,
  1600,
  2
};

const int MaxString = 4;
const int coodValNum = 4;
String inputString = "";
  long coor_x = 0;
  long coor_y = 0;
  long coor_z = 0;
  int speed_slow = 0;  // Langsam
  int speed_mid = 1;   // Mittel
  int speed_fast = 2;  // Schnell
  int speed = 0;
 // bool nextStepfast = false;
  bool finish = false;

  //bool Display_Wait = false;
  bool sendTextMoved = false;
  String strings[MaxString];


void setup() {

  //Motoren
  stepperX.setMaxSpeed(1000);
  stepperX.setAcceleration(1000);
  stepperX.setEnablePin(A4);
  stepperX.setPinsInverted(true, false, false);

  stepperY.setMaxSpeed(1000);
  stepperY.setAcceleration(1000);
  stepperY.setEnablePin(A6);

  stepperZ.setMaxSpeed(1000);
  stepperZ.setAcceleration(1000);
  stepperZ.setEnablePin(A8);

  // Setze digitale Pins

  //Notaus
  pinMode(Pins.Set_Notaus, OUTPUT);
  //Endschalter
  pinMode(Pins.LS_x1, INPUT);
  pinMode(Pins.LS_x2, INPUT);
  pinMode(Pins.LS_y1, INPUT);
  pinMode(Pins.LS_y2, INPUT);
  pinMode(Pins.LS_z1, INPUT);
  pinMode(Pins.LS_z2, INPUT);
  //Taster
  pinMode(Pins.Sw_x, INPUT);
  pinMode(Pins.Sw_y, INPUT);
  pinMode(Pins.Sw_z, INPUT);
  pinMode(Pins.Sw_v, INPUT);
  pinMode(Pins.Sw_Extra, INPUT);

  Serial.begin(115200);
  while (!Serial) {
    ;  // wait for serial port to connect. Needed for native USB port only
  }
  delay(500);
  Serial.println("Robot Online - Start to initialize");



  while (Serial.available() == false) { ; } // Für INB - Start erst nach Kommando

  digitalWrite(Pins.Set_Notaus, HIGH);
  // Suche den Nullpunkt

  Status.Notaus == false;
  DrivetoZero();
  getNotaus();
  delay(1000);

  // Starte Messung
  Meas_FOV_new();
  delay(1000);

  // Messung zu
  Robot_Status_Error("Error");
  delay(1000);
}

void loop() {
}

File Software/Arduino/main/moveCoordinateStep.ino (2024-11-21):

void moveCoordinatesStep(long x, long y, long z, int speed) {

  if (Status.Error == true || Status.Notaus == true)
  {
    // Es wird kein Step gemacht -> ErrorNachricht auf Display
    Robot_Status_Error("Final"); 
    return;
  }


  switch (speed) {
    case 0:  //langsam
      set_Stepper(500, 500);
      break;
    case 1:  //mittelschnell
      set_Stepper(1000, 1000);
      break;
    case 2:  //schnell
      set_Stepper(1000, 4000);
      break;
    default:  //default -> langsam
      set_Stepper(100, 100);
      break;
  }


  stepperX.moveTo(ConvertCoor(0, x, "R_Steps->S_Steps_XY"));
  stepperY.moveTo(ConvertCoor(0, y, "R_Steps->S_Steps_XY"));
  stepperZ.moveTo(ConvertCoor(0, z, "R_Steps->S_Steps_Z"));


  while (stepperX.distanceToGo() != 0 || stepperY.distanceToGo() != 0 || stepperZ.distanceToGo() != 0) {

    stepperX.run();
    stepperY.run();
    stepperZ.run();

    if (getLS("x") == true) {
    
      disableStepper("x");
      setError(true);
      Robot_Status_Error("Retry");  
      break;
    }

    if (getLS("y") == true) {
     
      disableStepper("y");
      setError(true);
      Robot_Status_Error("Retry");  
      break;
    }

    if (getLS("z") == true) {
     
      disableStepper("z");
      setError(true);
      Robot_Status_Error("Retry");      
      break;
    }

    if (digitalRead(Pins.Sw_Extra) == HIGH) {  // extra Button if needed
      Serial.println("  Cancel through User");
      disableStepper("x");
      disableStepper("y");
      disableStepper("z");
      setError(true);
      break;          
    }

// Check Emergency Switch
    if (getNotaus() == true) {
      disableStepper("x");
      disableStepper("y");
      disableStepper("z");
      setError(true);      
      Robot_Status_Error("Final");
      break;
    }
 
  }
    Status.posX = ConvertCoor(0, stepperX.currentPosition(), "S_Steps->R_Steps_XY");
    Status.posY = ConvertCoor(0, stepperY.currentPosition(), "S_Steps->R_Steps_XY");
    Status.posZ = ConvertCoor(0, stepperZ.currentPosition(), "S_Steps->R_Steps_Z");


}

void disableStepper(char Axis)
{
  if (strcmp(Axis, "x") == 0) {
    stepperX.stop();
    stepperX.disableOutputs();
  } else if (strcmp(Axis, "y") == 0) {
    stepperY.stop();
    stepperY.disableOutputs();
  } else if (strcmp(Axis, "z") == 0) {
    stepperZ.stop();
    stepperZ.disableOutputs();
  }
  
}

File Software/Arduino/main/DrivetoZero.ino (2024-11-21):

void DrivetoZero() {

  delay(1000);

  stepperX.move(-10000000);
  stepperY.move(-10000000);
  stepperZ.move(-10000000);

  set_Stepper(3000.0, 1500.0); // Mittelschnelles Bewegen des Roboters

  // Fahre zuerst die x-Achse
  while (1==1)
  {
    if (getLS("x") == false) //Endschalter in x ist nicht getriggert -> Weiter fahren
    {
      stepperX.run();
    }
    else { //Nullposition erreicht
      stepperX.stop();
      stepperX.move(100); //Fahre 100 Steps nach vorne, als Puffer
      stepperX.runToPosition();
      stepperX.setCurrentPosition(0); //Diese Position ist die 0 Positon vom Roboter
      break;
    }

  }

  // Fahre danach die y-Achse
  while (1==1)
  {
    if (getLS("y") == false) //Endschalter in x ist nicht getriggert -> Weiter fahren
    {
      stepperY.run();
    }
    else { //Nullposition erreicht
      stepperY.stop();
      stepperY.move(100); //Fahre 100 Steps nach vorne, als Puffer
      stepperY.runToPosition();
      stepperY.setCurrentPosition(0); //Diese Position ist die 0 Positon vom Roboter
      break;
    }

  }

  // Fahre als letzes die z-Achse
  while (1==1)
  {
    if (getLS("z") == false) //Endschalter in x ist nicht getriggert -> Weiter fahren
    {
      stepperZ.run();
    }
    else { //Nullposition erreicht
      stepperZ.stop();
      stepperZ.move(100*2); //Fahre 100 Steps nach vorne, als Puffer, z-Achse braucht doppelt so viele Steps
      stepperZ.runToPosition();
      stepperZ.setCurrentPosition(0); //Diese Position ist die 0 Positon vom Roboter
      break;
    }

  }

Status.posX = 0;
Status.posY = 0;
Status.posZ = 0;

}
